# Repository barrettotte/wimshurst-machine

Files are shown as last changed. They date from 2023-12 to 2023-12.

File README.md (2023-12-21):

# wimshurst-machine

A [Wimshurst machine](https://en.wikipedia.org/wiki/Wimshurst_machine) made to learn about electrostatic generators.

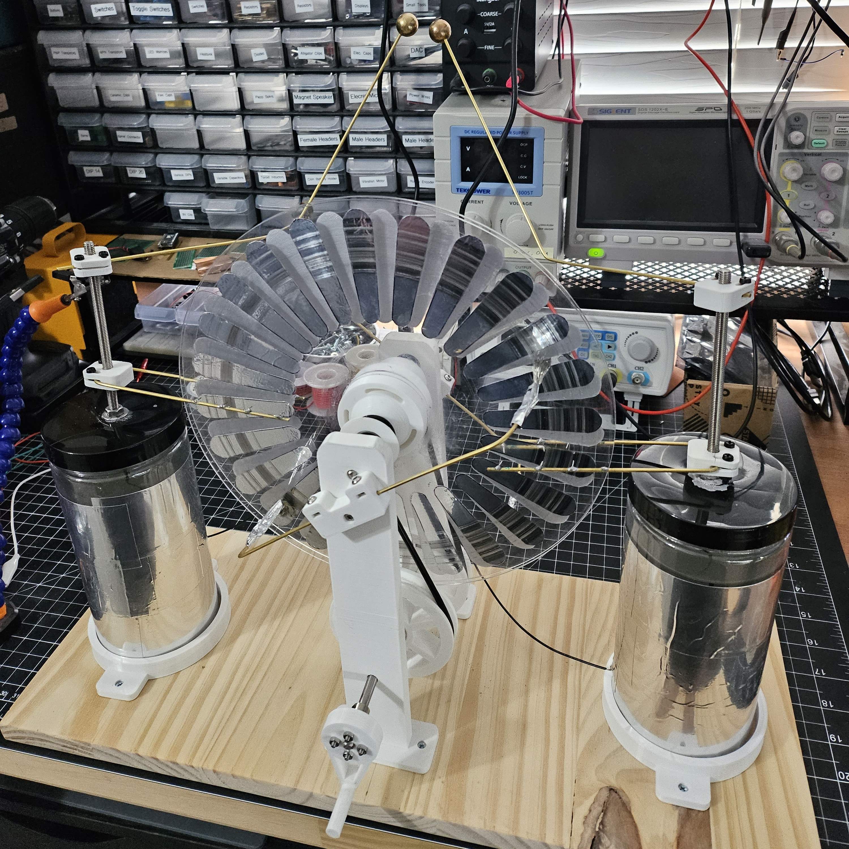
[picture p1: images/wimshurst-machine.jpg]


I had trouble recording it, but the best I could get was a half inch spark gap.
1 inch spark gap is about 30kV, so I guess I generated about 15kV.
I wish I could get a better spark gap, but I'm satisfied enough with the result and ready to move on.

## Parts List

- 2x [10 inch clear acrylic disc](https://www.amazon.com/gp/product/B09WB37JMC/)
- 6x [606 bearing](https://www.amazon.com/gp/product/B07FDZWK76)
- 2x [15mm brass bearing](https://www.amazon.com/gp/product/B0B5XKQNMR)
- 2x [M6 threaded rod](https://www.amazon.com/gp/product/B08FQR9CJW)
- 2x [M6 304 stainless steel rod](https://www.amazon.com/gp/product/B082ZNXYMG)
- 3x [6mm flange coupling conector](https://www.amazon.com/gp/product/B08334N261)
- 4x [2mm brass rod](https://www.amazon.com/gp/product/B087JYWMF9)
- 1x [4mm polyurethane belt](https://www.amazon.com/gp/product/B0BM3SCL12)
- 2x [Salwater leyden jars](https://github.com/barrettotte/bytes/tree/master/electrostatics/leyden-jar)
- 8x [Flat head #4 x 1/2"](https://www.amazon.com/gp/product/B08RW9BLG3)
- [3mm nylon bolts and nuts](https://www.amazon.com/gp/product/B076J5RGKS)
- [Aluminum foil tape](https://www.amazon.com/gp/product/B0BF3NGVDZ)
- 8" x 20" wood board
- 3D printed parts
  - 4x [cad/collector-mount.stl](cad/collector-mount.stl)
  - 2x [cad/disk-pulley.stl](cad/disk-pulley.stl)
  - 1x [cad/disk-spacer.stl](cad/disk-spacer.stl)
  - 2x [cad/drive-pulley.stl](cad/drive-pulley.stl)
  - 1x [cad/electrode-template.stl](cad/electrode-template.stl)
  - 1x [cad/hand-crank.stl](cad/hand-crank.stl)
  - 2x [cad/leyden-jar-mount.stl](cad/leyden-jar-mount.stl)
  - 2x [cad/neutralizer-v2.stl](cad/neutralizer-v2.stl)
  - 2x [cad/support-bottom.stl](cad/support-bottom.stl)
  - 2x [cad/support-top.stl](cad/support-top.stl)

## Build Notes

This project got away from me...I meant to write down each step as I built it. 
But, building this took longer than I expected and I got distracted by other projects.
So, this next part is not very helpful.

I used mainly M3 nylon bolts and nuts to prevent charge from leaking out.
Unfortunately, I was not smart enough to actually write down the bolt lengths I used and they are not really reflected in my design. 
I need to get better about adding this type of stuff to my Fusion 360 projects.

For each support, I press fit a [606 bearing](https://www.amazon.com/gp/product/B07FDZWK76) 
into [cad/support-bottom.stl](cad/support-bottom.stl) and [cad/support-top.stl](cad/support-top.stl).
Then I superglued them together.

For each disk, I used a [10 inch clear acrylic disc](https://www.amazon.com/gp/product/B09WB37JMC/) and drilled a 6mm hole in the center.
I used [cad/electrode-template.stl](cad/electrode-template.stl) to trace an outline for 24 electrodes on aluminum foil tape.
Then I positioned them equally around the disk using a protractor.

The axles were cut from [M6 304 stainless steel rod](https://www.amazon.com/gp/product/B082ZNXYMG).
The top axle is ~13mm and the bottom axle is ~20mm.

For each disk pulley, I press fit a [606 bearing](https://www.amazon.com/gp/product/B07FDZWK76) into [cad/disk-pulley.stl](cad/disk-pulley.stl) 
and super glued it to a disk. Each [cad/disk-pulley.stl](cad/disk-pulley.stl) is mounted to the top axle.

The drive belts are made from [4mm Polyurethane belt](https://www.amazon.com/gp/product/B0BM3SCL12).
I cut them to size (forgot to record this) and used a soldering iron to re-weld the belts.
One belt has a twist in it, to ensure the belts rotate in opposite directions.

For each drive pulley, I mounted it to the bottom axle using a [6mm flange coupling conector](https://www.amazon.com/gp/product/B08334N261).
The belts are setup between each [cad/disk-pulley.stl](cad/disk-pulley.stl) and [cad/drive-pulley.stl](cad/drive-pulley.stl).

The [cad/hand-crank.stl](cad/hand-crank.stl) is fixed to the bottom axle 
using a [6mm flange coupling conector](https://www.amazon.com/gp/product/B08334N261).

For each collector, I bent [2mm brass rod](https://www.amazon.com/gp/product/B087JYWMF9) in a U shape 
and soldered small spikes of wire pointing inside. 
This bent rod gets clamped into [cad/collector-mount.stl](cad/collector-mount.stl) using nylon bolts and nuts.

For each neutralizer, I bent [2mm brass rod](https://www.amazon.com/gp/product/B087JYWMF9) and clamped it into
[cad/neutralizer-v2.stl](cad/neutralizer-v2.stl) using nylon bolts and nuts.
Then I taped stranded wire to each end of the neutralizer using aluminum foil tape.

For each electrode, I bent [2mm brass rod](https://www.amazon.com/gp/product/B087JYWMF9) and clamped it into
[cad/neutralizer-v2.stl](cad/neutralizer-v2.stl) using nylon bolts and nuts.
I drilled a ~2mm partial hole into each [15mm brass bearing](https://www.amazon.com/gp/product/B0B5XKQNMR) and
super glued it to the end of the bent rod.

For each leyden jar, I built a saltwater leyden jar using my instructions 
in [bytes/electrostatics/leyden-jar](https://github.com/barrettotte/bytes/tree/master/electrostatics/leyden-jar).
To ensure position, the leyden jar is placed in a [cad/leyden-jar-mount.stl](cad/leyden-jar-mount.stl).
A wire is also connected between each leyden jar on the outside foil.

## Related

Other things I made while building the Wimshurst machine.

- [Electrophorus](https://github.com/barrettotte/bytes/tree/master/electrostatics/electrophorus)
- [Electroscope](https://github.com/barrettotte/bytes/tree/master/electrostatics/electroscope)
- [Leyden Jar](https://github.com/barrettotte/bytes/tree/master/electrostatics/leyden-jar)

## References

- [History of Electrostatic Generators](http://www.hp-gramatke.net/history/english/page4000.htm)
- https://en.wikipedia.org/wiki/Wimshurst_machine
- [How a Wimhurst Machine Works; RimstarOrg](https://www.youtube.com/watch?v=nA4aCd5qFWs)
- https://spectrum.ieee.org/wimshurst-machine
- https://hackaday.com/2017/03/03/how-wimshurst-machines-work-high-voltage-from-the-gods/

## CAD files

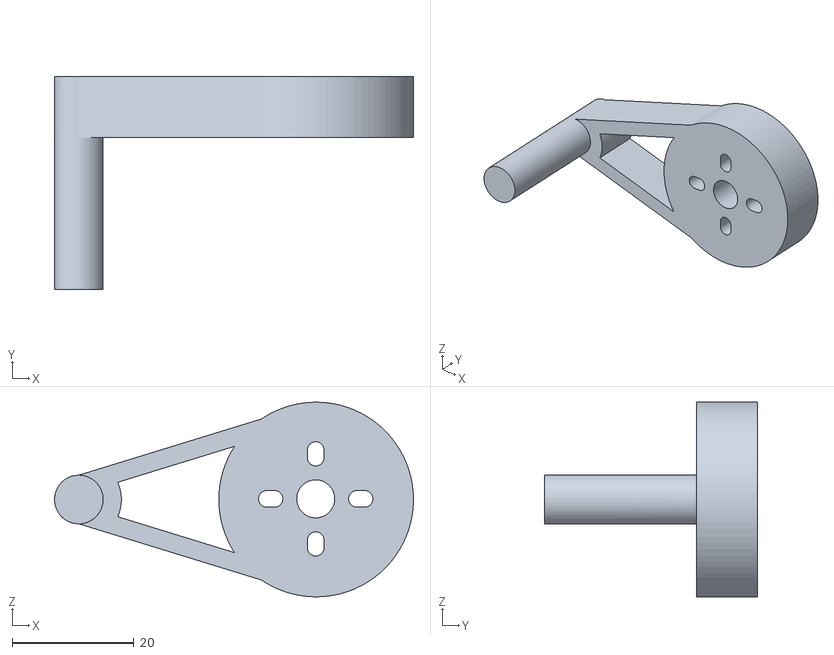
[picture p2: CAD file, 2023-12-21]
cad/hand-crank.stl
59.0 x 35.0 x 32.0

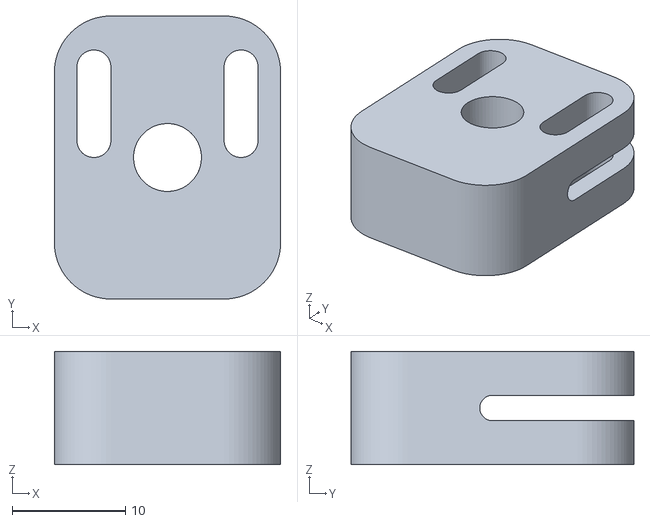
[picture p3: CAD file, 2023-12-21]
cad/collector-mount.stl
20.0 x 25.0 x 10.0

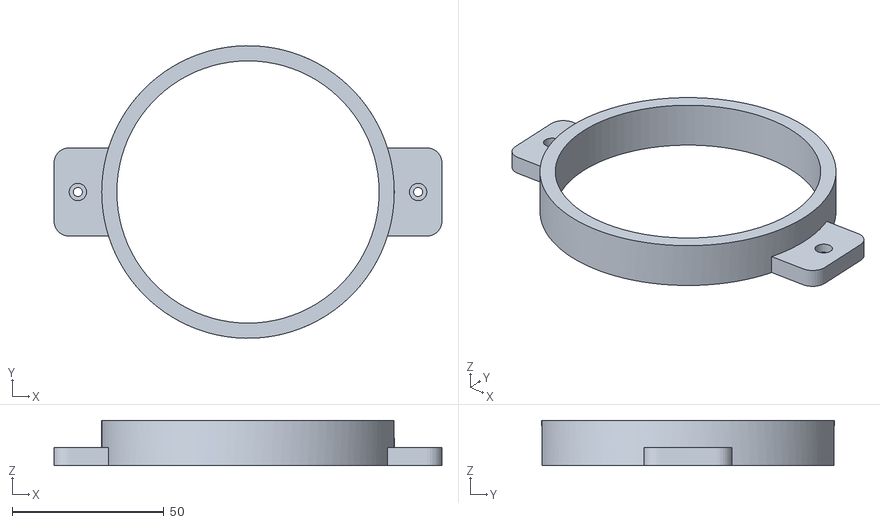
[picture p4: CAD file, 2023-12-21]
cad/leyden-jar-mount.stl
128.1 x 96.5 x 15.0

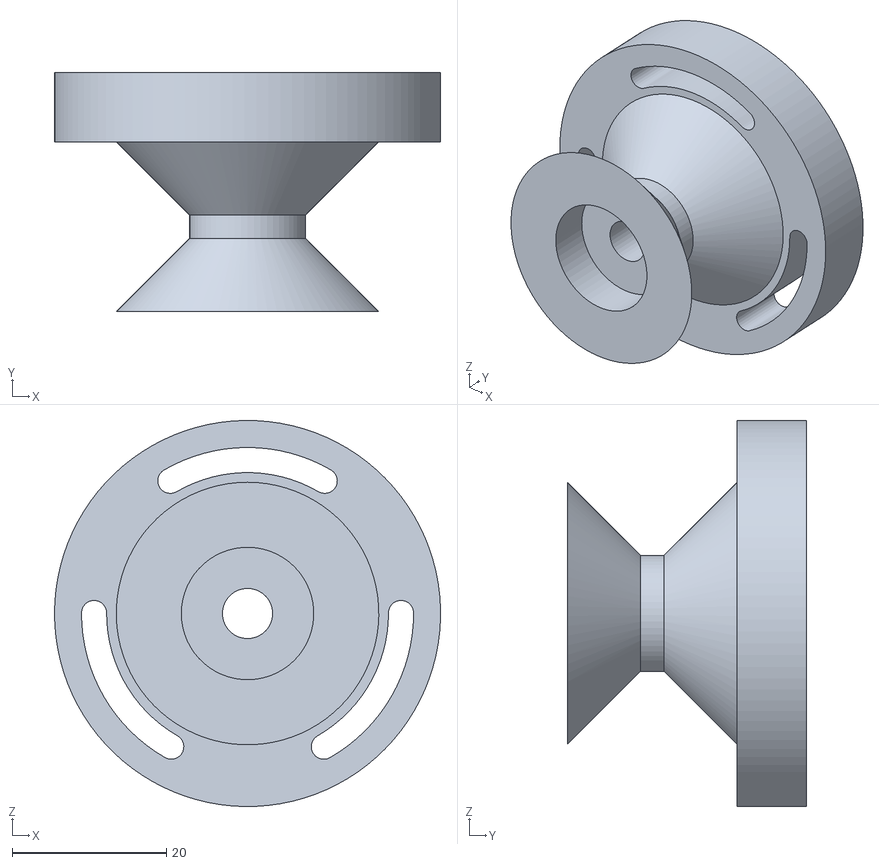
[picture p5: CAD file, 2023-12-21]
cad/disk-pulley.stl
50.0 x 31.0 x 50.0

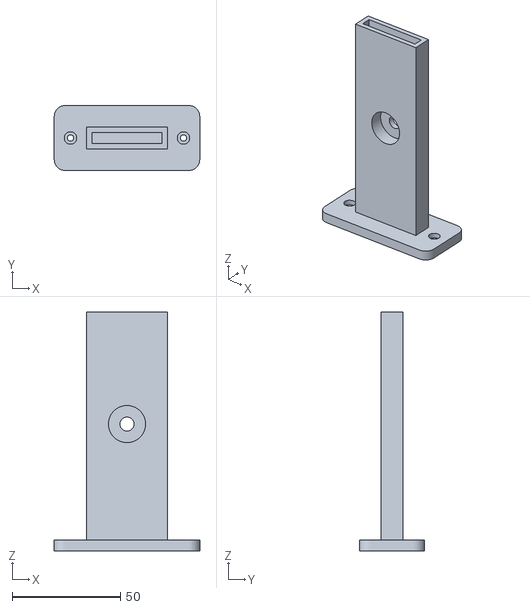
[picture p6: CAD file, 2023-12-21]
cad/support-bottom.stl
67.2 x 30.0 x 110.3

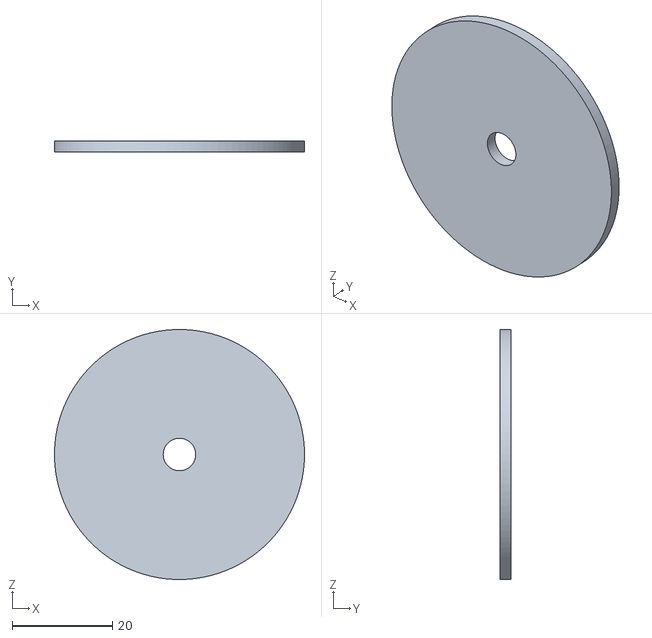
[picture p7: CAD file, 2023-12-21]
cad/disk-spacer.stl
50.0 x 2.25 x 50.0

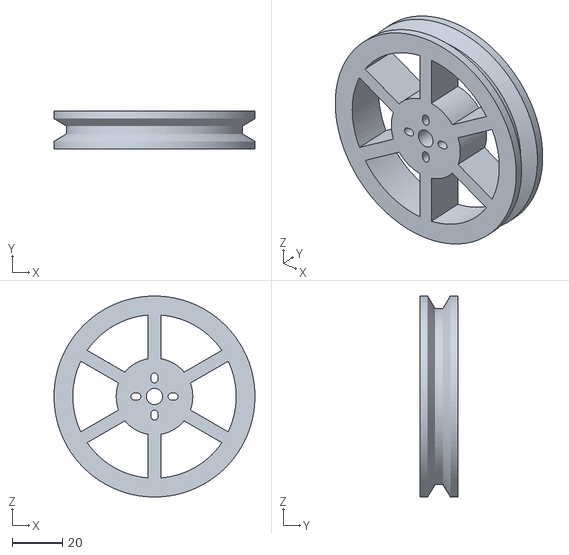
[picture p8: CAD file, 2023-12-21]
cad/drive-pulley.stl
80.0 x 15.0 x 80.0

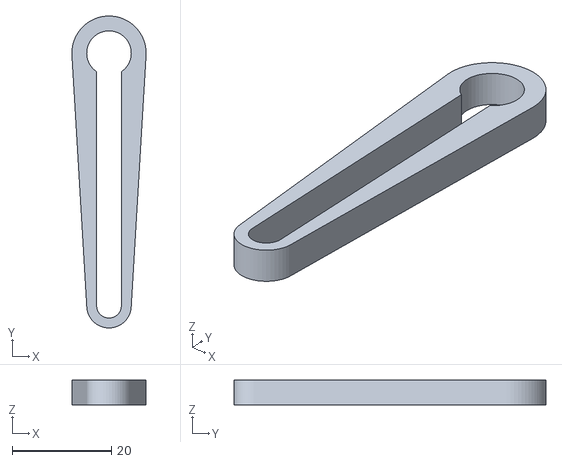
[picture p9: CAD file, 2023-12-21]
cad/electrode-template.stl
15.0 x 63.0 x 5.00

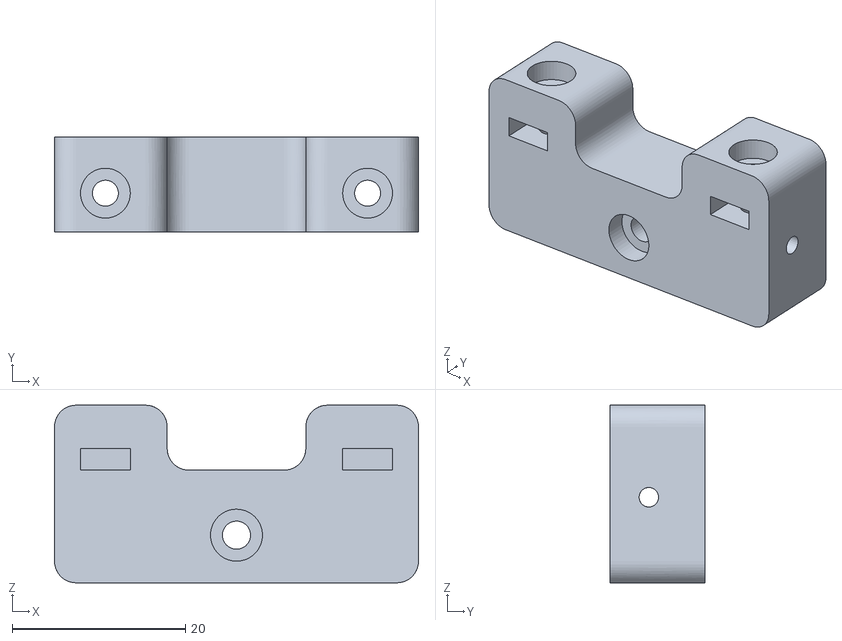
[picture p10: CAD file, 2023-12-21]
cad/neutralizer-v2.stl
42.0 x 11.0 x 20.5

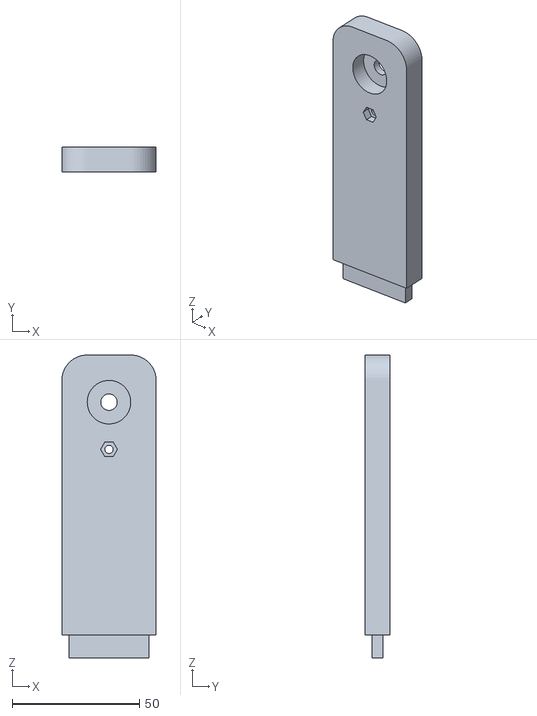
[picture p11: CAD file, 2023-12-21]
cad/support-top.stl
37.2 x 10.0 x 119.3

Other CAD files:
cad/wimshurst-machine.f3d
